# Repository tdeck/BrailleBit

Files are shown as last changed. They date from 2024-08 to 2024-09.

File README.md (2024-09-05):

# BrailleBit - An Arduino braille display

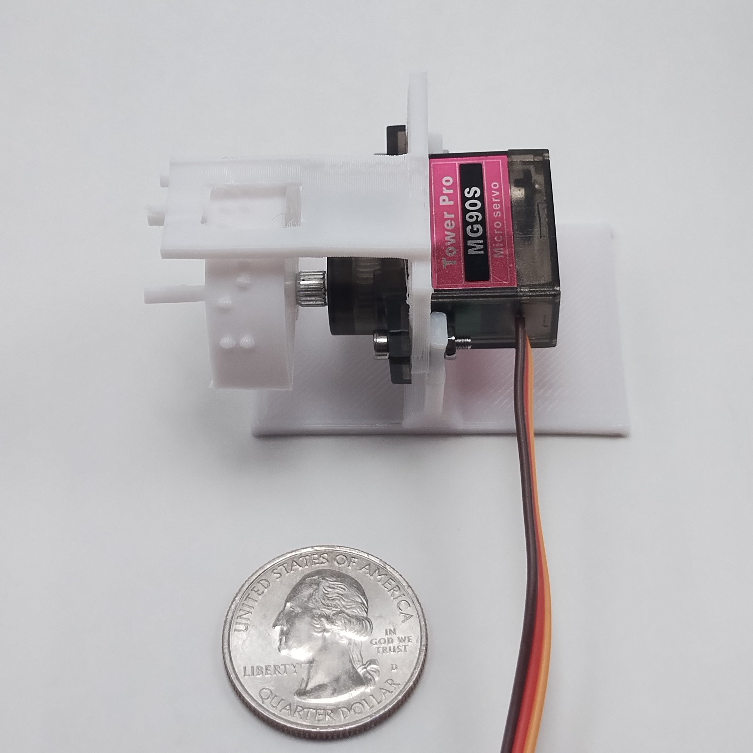
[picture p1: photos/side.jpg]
BrailleBit photo; side

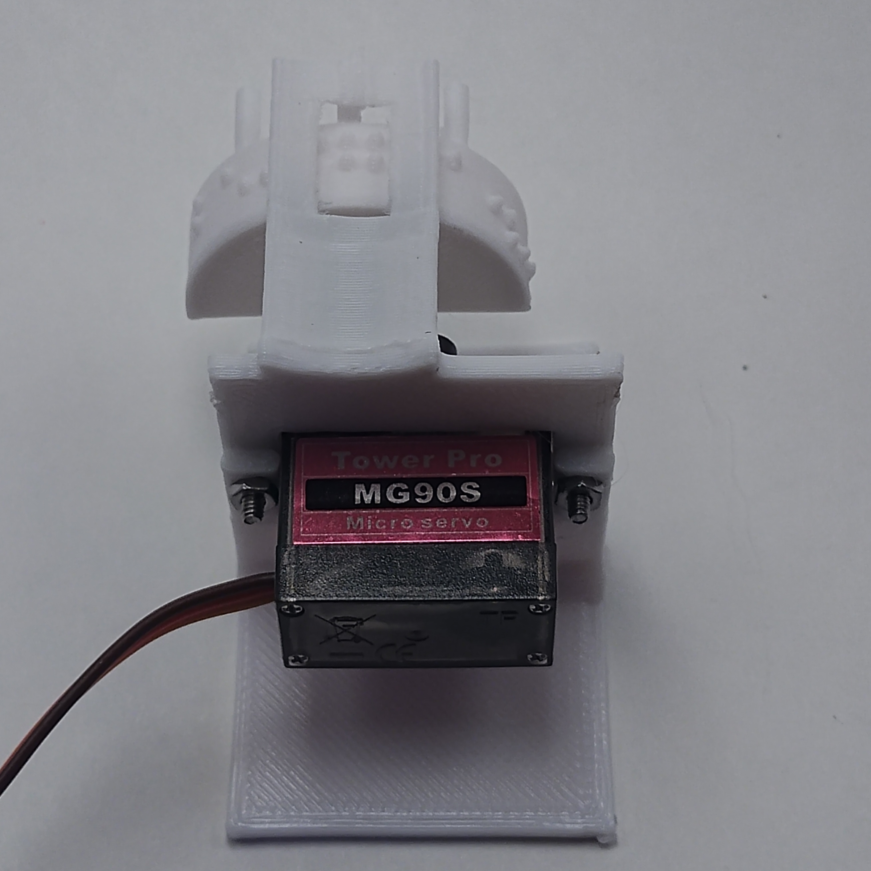
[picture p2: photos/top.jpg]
BrailleBit photo; top


The BrailleBit is an easy way to add a single cell of braille output to your Arduino project. It's cheap and cheerful - using only a hobby servo and 2 or 3 small 3D-printed parts. It costs less than $5, displays standard-sized braille, works with almost any microcontroller, and can be assembled and calibrated by touch. The main drawback is that it's too large to fit multiple cells side-by-side, and has a limited character set. Think of this as an alternative to a 7-segment module, not a replacement for a 2 line LCD.

The hardware is controlled with a simple Arduino library. For example, here's a sketch that repeatedly counts from 0 to 9 with a BrailleBit attached on pin 1:

```cpp
const int SERVO_PIN = ...;

// These come from servo calibration
const uint16_t US_PER_4DEG = ...;
const uint16_t US_CENTER = ...;

const uint16_t US_PER_4COL = US_PER_4DEG * NumericRotor::DEGREES_PER_DOT;
BrailleBit brailleBit(NumericRotor::CHARS);

void setup() {
    brailleBit.attach(SERVO_PIN, US_CENTER, US_PER_4COL);
}

void loop() {
    char* sequence = " 0123456789";

    for (char* ptr = message; ptr != 0; ++ptr) {
        cell.setChar(*p);
        delay(2000);
    } 
}
```

## Physical description

The BrailleBit has a small window through which you can feel two columns of braille dots. Behind this window is the rotor, which is a semicircular plastic piece that has columns of 3 dots in different combinations along its outside wall. A small servo motor allows the BrailleBit to precisely rotate the rotor to expose two adjacent columns of dots at a time. By cleverly arranging the combinations of dots on the rotor's outer wall, we make it possible to display different Braille symbols. The basic BrailleBit is designed for numeric output; it supports letters A-J (for digits 0-9 in braille), the period, minus sign, space, and colon. The result is a device that is about 3.5 cm wide, 6 cm long, and stands 4 cm high on a desk.

The minimalist design of the BrailleBit is a starting point for your own projects and designs. At its simplest, you need the 3D printed rotor and the 3D printed "cover bracket", which provides the fixed window and attaches to a common hobby servo. The base support bracket allows you to place the BrailleBit flat on a desk, with the reading window parallel to the desktop. You can also omit the base bracket and mount the BrailleBit in other ways. For example, you could cut a hole larger than the BrailleBit window in a box, then glue the cover bracket against that hole from the inside.

The provided BrailleBit rotor supports numeric output only. Larger rotors could accommodate more letters, although the process of creating new rotors is not documented yet. A full 26 letter rotor has problems with the mechanical backlash within the servo which I am still working to overcome.

## Parts needed

Here's everything you'll need:

- 3D-printed rotor (prints/rotor.stl)
- 3D-printed cover bracket corresponding to rotor (prints/cover_bracket.stl)
- 3D-printed support bracket (prints/support_bracket.stl) (this is optional, you could mount the BrailleBit another way)
- 2x M2 screws, suggested length 10mm
- 2x m2 nut
- MG90S (or clone) micro servo
- M2.5 5mm screw for servo shaft (this should come with your servo)
- Arduino or compatible microcontroller board

Hardware stores typically don't carry very small screws like this. If you're in the US, I've found [Trimcraft Aviation](http://trimcraftaviation.com/) is a great place to buy small metric fasteners for very little money. M2 screws and nuts are extremely small so it's a good idea to have extras in case you drop one and can't find it again.

The MG90S servo was originally designed by Tower Pro; although there are now many clones available for less than $1 per piece on sites like eBay, Aliexpress, and Banggood. Usually it's more economical to buy a multi-pack. Note that you may end up with a bad batch that drifts or has other problems so consider the cost an your risk tolerance.

### If you don't have a 3D printer

3D printers are common these days at many institutions, including schools and public libraries. There may be one you can use or a service where they'll print things for you for free at these institutions. These parts can be printed on a basic filament 3D printer.

If you are Blind or an educator for Blind people, you may be able to ask the good folks at [See3D](https://see3d.org/) to print these parts for you. Be sure to send them a link to these instructions so they can read the printing notes below.

### Printing notes

Print all parts in their provided orientations.

When slicing the rotor, be sure that the Braille dots are being printed as ripples in the print's outer wall, rather than extra segments attached to the outside. I found that in Cura it was helpful to set the wall thickness to .8mm. I also found printing with thinner layers (.1mm) beneficial for the rotor. Print the rotor without supports.

For the cover bracket, you can print with relatively coarse layers. I recommend enabling supports to fill the window rather than relying on bridging, since the extra material is minimal.

For the support bracket, you don't need any support and can print fast.

## Assembly guide

1. Thread one of the M2 screws through one of the servo's mounting holes so the shaft of the screw points toward the wire end of the servo and away from the rotor.

2. Align the cover bracket with the servo. The servo's shaft is not symmetrical - it is closer to one side of the servo than the other. This is also true of the cover bracket. Slide the cover bracket around the servo and over the protruding screw so that the window in the cover is horizontally aligned with the shaft of the servo. The screw you inserted in step 1 should now pass through the servo mount and then the cover bracket. 

3. If using the base support bracket, slip it onto the screw behind the cover bracket.

4. Attach a nut to the screw and tighten, pushing the bracket(s) so they're flush with the body of the servo.

5. Add the second M2 screw and M2 nut to the other mounting hole and bracket(s) and tighten.

6. With the rotor flat on the table and the semicircular wall pointing upward, insert the servo rotor screw downward into the hole in the rotor. Lift the rotor so the screw pokes through.

7. Screw the protruding rotor screw into the servo shaft and tighten lightly. You make a final adjustment to this screw during the calibration process.

## Attaching the servo to your Arduino (or other microcontroller)

The MG90s servo requires no support circuitry to work with an Arduino. Specifically, you can connect the servo's PWM output directly to a pin on your Arduino that supports PWN, whether 3.3v or 5v. [This page](https://support.arduino.cc/hc/en-us/articles/9350537961500-Use-PWM-output-with-Arduino) lists PWM pins for official Arduino boards; for RP2040 boards like the Pi Pico all pins support PWM.

The servo needs an independent power source. I've had success powering it from the 5 volt USB supply on development boards, but to do this you'll need to account for the large spikes in current draw the servo takes when it moves. A 470 microfarad electrolytic capacitor across the power pins for the servo did the job for me, but if you're having trouble I suggest using a bench power supply at 5 or 6 volts.

### Identifying servo pins

The MG90S has a 3-pin female connector. Near the end of the connector there are 3 small notches on one side, while the other side is flat. With the notched side facing you and the connector pointing down, the pins from left to right are:

- Left (brown): Ground
- Middle (red): Power
- Right (orange): PWM input

Note if you get this backwards, the servo will not work but it also won't be damaged.

## Calibration guide

Calibrating your BrailleBit is necessary before you first use it and after you unscrew or swap the rotor. It's a quick procedure but does require a phillips head screwdriver, a connected Arduino, and 3 pushbuttons wired to I/O pins on the Arduino. Calibration will provide you with two constants `US_CENTER` and `US_PER_4DEG` that are required to control the BrailleBit.

Begin by loading the calibration sketch in the Arduino IDE (firmware/calibration/calibration.ino). You will need to update all pin assignment the constants at the top of the file (SERVO_PIN, LEFT_BUTTON_PIN, CONTINUE_BUTTON_PIN, and RIGHT_BUTTON_PIN).

Wire 3 pushbuttons between V+ and 3 different I/O pins, so that they pull the pins up when pressed. If you're using an RP2040 based board like the Pi Pico you may need external pulldown resistors since the internal ones don't seem to work. As you attach the buttons, update the Arduino sketch to note what pins they're attached to. Wire the servo PWM pin to a free PWM pin (see above) and update that constant as well. Be sure to keep track of which button is "left", "right", and "continue".
 
Upload the sketch to the board and open the serial monitor on your computer. The servo should move, and you'll get a message on the serial monitor telling you to set the center position. The calibration sketch lets you know what mode it's in on the serial console.

The rotor has three little poles sticking up from it, and there's a small tab or spike in the middle of the cover bracket above the window. The goal of the calibration procedure is to teach the Arduino how to line up these tabs.

First, mechanically center the rotor. While the sketch is holding the servo in its default position, partly unscrew the rotor. Hold the *center* tab of the rotor and turn it so it's against the tab on the cover window. Holding these together, tighten the rotor screw firmly. Do not unscrew the rotor again for the rest of the process. Do not skip the mechanical alignment step - the servo cannot rotate a full 360 degrees so we must align the rotor to its range of motion.

It's likely the alignment won't be perfect at this point, so use the left and right buttons to electronically move the rotor until the tabs are aligned as well as you can make them (the smaller window tab should be roughly centered on the rotor tab). At this point you're in coarse alignment mode and the motor will take larger steps. Pressing continue places you in the fine alignment mode where you can fine tune the alignment with smaller steps.

When you have pressed "continue" in the center coarse and fine alignment modes, the servo will swing to where it guesses the left alignment tab will be. Use the left and right buttons to align it to the left tab as well as you can in coarse mode, then press continue to enter fine mode and fine tune it.

When you press "continue" again the servo will swing into position for the final 2 alignment steps - the right coarse and fine alignment.

After you're satisfied with the alignment of the right calibration tab, press the continue button one last time. At this point the calibration sketch will start repeatedly printing values of US_CENTER and US_PER_4DEG to the serial console. Copy these values and save them - they are the goal of the calibration. If you have a problem, you can always power-cycle the Arduino and redo the calibration.

Just as a recap, here are the stages you'll go through in calibration.

1. Center coarse alignment
2. Center fine alignment
3. Left coarse alignment
4. Left fine alignment
5. Right coarse alignment
6. Right fine alignment
7. Output

### Alternatives to the serial console

If your device has no working serial console, there are 2 other ways to get the calibration constants. These can be selected by uncommenting the USE_READOUT_xxx constants in calibration.ino. If your device has EEPROM, you can uncomment USE_READOUT_EEPROM and set a value for EEPROM_WRITE_ADDRESS. The calibration routine will write in two bytes US_CENTER at that address, and US_PER_4DEG two bytes later. You can then use the [EEPROM library](https://docs.arduino.cc/learn/built-in-libraries/eeprom/) to read these values out on the same Arduino board.

Another rather inconvenient option is Morse code. Uncommenting the USE_READOUT_MORSE will cause the servo to dart left to right, sending Morse code. A short dart to the left is a dit (a Morse dot), and a longer dart to the right is a dah (Morse dash). In Morse mode the completed calibration sketch will loop endlessly, sending the morse letter C, then the digits for US_CENTER, then a D, then US_PER_4DEG. Learning morse is beyond the scope of this short tutorial.

## Controlling the BrailleBit

The BrailleBit comes with a simple control library. For now it's not in the Arduino library manager, so start your sketch by copying the code in the firmware/control folder of this repository. That code shows you how to import the BrailleBit and use it in your own projects.

The BrailleBit objects have two control commands: `displayChar()` and `setChar()`. The `setChar()` method simply moves the rotor to the specified character, and if the character hasn't changed it won't move. The `displayChar()` is a bit smarter - if the character is the same as the last one, it will jiggle the servo slightly. This provides important feedback so you can distinguished repeated characters (e.g. "1001" should look different from "101").

You can display more than one character in a couple of ways. The simples is to put a delay between each character output, which is what the example sketch does. A nicer option is to wire up a button that lets you move on to the next character, so that you can suit different users' reading speeds.

## Get in touch!
If you create something cool with the BrailleBit, or have any questions or comments, email me at troy@blindmakers.net. You can also open issues on this GitHub repository. I'd love to share and link to any other creations.

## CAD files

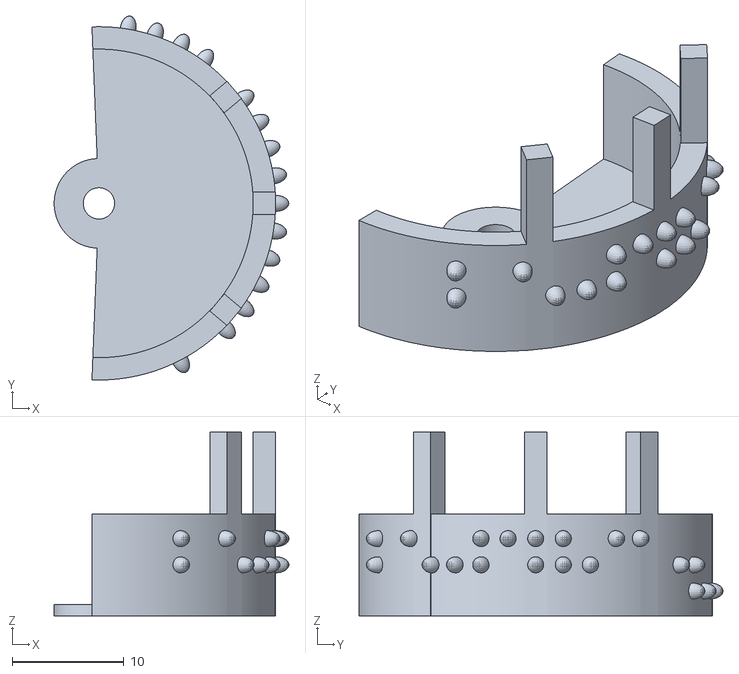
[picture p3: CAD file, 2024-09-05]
prints/rotor.stl
21.0 x 32.5 x 16.4

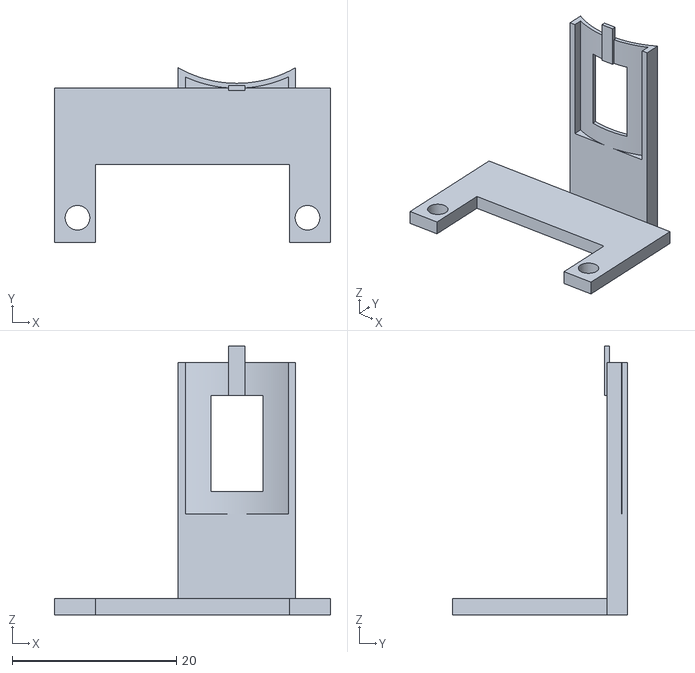
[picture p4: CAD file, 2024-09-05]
prints/cover_bracket.stl
33.6 x 21.3 x 32.7

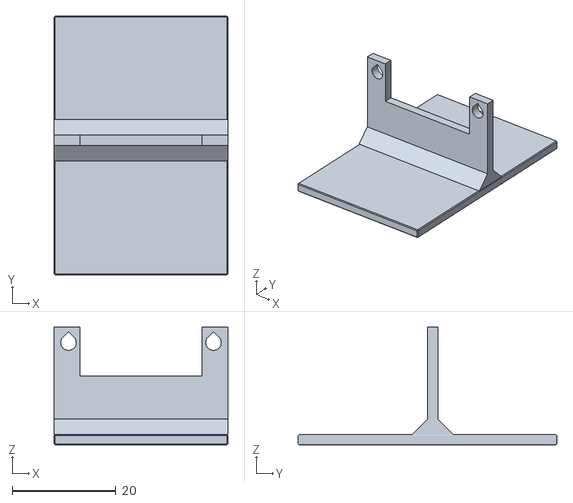
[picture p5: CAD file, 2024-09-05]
prints/support_bracket.stl
33.6 x 50.0 x 22.8

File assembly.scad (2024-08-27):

include <common.scad>

// These movements and rotations just line the assemblies up so their relationship shows up in the preview
forward(radius_of_whole_circle + COVER_ROTOR_GAP)
    right(SERVO_ROTOR_OFF_CENTER)
    up(SERVO_ROTOR_TOP_TO_SCREW_PLATE_BOTTOM)
    down(USE_SERVO_SPLINE ? SERVO_SPLINE_ATTACHMENT_HEIGHT :  0)
    zrot(90)
        braille_rotor();
cover_bracket();

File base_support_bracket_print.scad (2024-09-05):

include <common.scad>

xrot(-90)
base_support_bracket();

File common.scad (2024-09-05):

include <BOSL/constants.scad>
use <BOSL/transforms.scad>
use <BOSL/shapes.scad>

// The next long line was generated from a Python script and represents the arrangement of 3-dot columns on the rotor wall
// All possible cells
//DOT_COLUMNS = [[0,0,0],[1,0,0],[0,1,1],[0,0,1],[0,0,0],[1,1,1],[0,0,1],[1,0,1],[0,1,1],[1,1,1],[1,0,1],[1,0,0],[1,1,0],[1,1,1],[1,1,0],[0,0,0],[0,0,1],[1,1,0],[1,0,1],[1,0,1],[0,0,0],[0,1,1],[1,0,1],[1,1,0],[0,1,0],[0,1,0],[1,0,0],[1,0,1],[0,0,1],[1,1,1],[1,0,0],[0,0,0],[1,1,0],[1,1,0],[0,0,1],[1,0,0],[0,1,0],[1,0,1],[0,1,0],[0,0,1],[0,0,1],[0,1,1],[0,1,1],[1,0,0],[0,0,1],[0,1,0],[1,1,0],[0,1,1],[1,1,0],[1,0,0],[1,0,0],[1,1,1],[1,1,1],[0,1,1],[0,1,0],[0,1,1],[0,0,0],[0,0,0],[1,0,1],[1,1,1],[0,0,0],[0,1,0],[1,1,1],[0,1,0],[0,0,0]];
// Alpha + basic punctuation
//DOT_COLUMNS = [[0,0,0],[0,0,1],[1,1,1],[0,0,0],[0,0,0],[0,1,1],[0,0,1],[0,0,1],[1,1,1],[0,1,0],[0,1,1],[1,1,0],[0,0,0],[0,1,0],[0,0,0],[1,0,1],[0,1,0],[1,1,0],[1,0,0],[0,1,0],[1,0,0],[1,0,0],[1,1,0],[1,1,0],[0,1,0],[1,1,1],[1,0,0],[0,0,0],[1,0,1],[1,0,1],[1,1,1],[1,1,0],[1,0,1],[1,1,0],[1,0,1],[1,0,0],[1,0,1],[0,1,1],[1,0,0],[1,1,1],[0,0,1],[1,0,1],[0,0,0],[1,0,1],[0,0,1]];

// Numeric
//DOT_COLUMNS = [[0,0,0],[0,0,0],[1,1,0],[0,1,0],[1,0,0],[1,0,0],[0,1,0],[0,1,1],[1,0,0],[1,1,0],[1,1,0],[0,0,0],[0,1,0],[1,1,0],[1,0,0],[0,0,0],[0,0,1],[0,0,1]];

// Numeric with colon
DOT_COLUMNS = [[0,0,0],[0,0,0],[1,1,0],[0,0,0],[1,0,0],[0,1,0],[0,1,0],[1,1,0],[1,0,0],[1,1,0],[1,1,0],[0,1,0],[1,0,0],[1,0,0],[0,0,0],[0,1,0],[0,1,1],[0,0,1],[0,0,1]];

// All dots filled, variable size for debugging
//DOT_COLUMNS =  [for(i=[1:5])([1,1,1])];

// Braille dimensions
DOT_HEIGHT = 1.2;  // Official is .48 but that's hard to feel, so I used the max height from California sign standards
DOT_DIAM = 1.44;
DOT_SPACING = 2.34; // Center to center

// DEGREES_TO_POPULATE specifies how much of the circle's arc can be "addressed" by the servo.
// I recommend adding a buffer zone so that the disc doesn't have to be perfectly aligned to the servo's movement
// region (e.g. for a 180 degree servo a 170 degree DEGREES_TO_POPULATE lets yo fix a 10 degree difference in
// software calibration rather than in hardware.
DEGREES_TO_POPULATE = 170;

// Rotor stuff
BLANK_SPACE_AT_END = 2; // Blank space to leave before first col and after last col on wheel (set to 0 for 360 deg)
V_PADDING = 1.5;
ROTOR_WALL_THICKNESS = 2;

// Backlash spring stuff
USE_BACKLASH_SPRING = false; // True is recommended unless your servo has very little play or your rotor radius is small
BACKLASH_SPRING_HORN_LENGTH = 15;
BACKLASH_SPRING_HORN_WIDTH = 6;

// Servo stuff
SERVO_RECT_HOLE_WIDTH = 23.6;
SERVO_RECT_HOLE_DEPTH = 13.0;
SERVO_HOLE_TO_SCREW_HOLE_CENTER = 2.2;
SERVO_MOUNTING_SCREW_HOLE_DIAM = 3.0;
SERVO_ROTOR_OFF_CENTER = 5.4;
SERVO_ROTOR_TOP_TO_SCREW_PLATE_BOTTOM = 11.9 + 2.4;
SERVO_HUB_SCREW_HOLE_DIAM = 2.8; // Should be a little on the small side so screw holds the rotor snugly
SERVO_SPLINE_TEETH = 20;
SERVO_SPLINE_TOOTH_DEPTH = .3;
SERVO_SPLINE_OUTER_DIAMETER = 4.9;
SERVO_SPLINE_CLEARANCE = .16; // Adjust this if your print doesn't fit
SERVO_SPLINE_ATTACHMENT_HEIGHT = 4;
SERVO_SPLINE_ATTACHMENT_WALL = 3; // Not exact, make a bit larger than it needs

// TODO the spline doesn't fit reliably when printed; explore attaching to servo horns
USE_SERVO_SPLINE = USE_BACKLASH_SPRING; // Recommended if you use the backlash spring; makes centering a little more difficult

// Window/cover stuff
COVER_RADIUS = 15;
COVER_WALL_THICKNESS = .6;
COVER_WINDOW_WIDTH = DOT_SPACING * 2.7;
COVER_WINDOW_HEIGHT = DOT_SPACING * 5;
COVER_WALL_ABOVE_WINDOW = 4;
COVER_WALL_BESIDE_WINDOW = 4; // This is not permiter length, it's cartesian
COVER_ROTOR_GAP = 0; // Extra gap between end of dots and start of cover with window in it
COVER_BRACKET_THICKNESS = 2;
COVER_FOOT_DEPTH = 5; // TODO figure out what this really means; it doesn't seem to be using the full 5
COVER_FOOT_HEIGHT = SERVO_ROTOR_TOP_TO_SCREW_PLATE_BOTTOM - 2;
COVER_BRACKET_LEN_PAST_SERVO_CENTER = 3;
COVER_BRACKET_LEN_PAST_SERVO_SIDES = 5;
COVER_BRACKET_WIRE_NOTCH_DEPTH = 2;
COVER_BRACKET_WIRE_NOTCH_WIDTH = 4;
COVER_SIDE_PILLAR_SIZE = 1.8;  // TODO make this not need trial and error

assert(COVER_BRACKET_WIRE_NOTCH_DEPTH < COVER_BRACKET_LEN_PAST_SERVO_SIDES);

// Floor
ROTOR_FLOOR_THICKNESS = 1;
ROTOR_HUB_RADIUS = 4;

// Calbiration tabs
USE_CALIBRATION_TABS = true; // This adds a little bit of plastic but makes aligning and calibrating your servo 10 times easier
CALIBRATION_TAB_ANGLE = 40;
CALIBRATION_TAB_HEIGHT = 2; // This is height above the window; height above the rotor will be greater
CALIBRATION_TAB_WIDTH = 2;
ROTOR_CALIBRATION_TAB_DEPTH = 2;

BOTTOM_CHAMFER_WIDTH = .2; // Used in some places to avoid elephants foot

// Support bracket
SUPPORT_BRACKET_EXTRA_HEIGHT = 2;
SUPPORT_BRACKET_BASE_LENGTH = 50;
SUPPORT_BRACKET_CHAMFER = 3; // Added in addition to the width of the wall

// Utility constants
ARBITRARY = 1000; // Arbitrary size for various hole dimensions
SMALL_DELTA = .01; // Small movement to resolve ambiguity when part edges overlap

 // Set global params for smoother shapes
$fa = 1;
$fs = .2;

// Computed constants
perimeter_needed_for_dots = (len(DOT_COLUMNS) + 1) * DOT_SPACING; // DOT_SPACING is center-to-center
perimeter_of_whole_circle = perimeter_needed_for_dots * 360 / DEGREES_TO_POPULATE;
radius_of_whole_circle = perimeter_of_whole_circle / PI / 2;
cell_height = 2*DOT_SPACING + DOT_DIAM;
rotor_height = cell_height + 2*V_PADDING;
cover_width = COVER_WINDOW_WIDTH + 2 * COVER_WALL_BESIDE_WINDOW;
cover_wall_above_rotor = COVER_WALL_ABOVE_WINDOW - (rotor_height - COVER_WINDOW_HEIGHT) / 2;

echo("len(DOT_COLUMNS)", len(DOT_COLUMNS));

module servo_spline_carveout(clearance=SERVO_SPLINE_CLEARANCE) {
    // This isn't a partuclarly well modeled socket for the servo spline but it manages
    // to work anyway
    spline_circumference = PI * SERVO_SPLINE_OUTER_DIAMETER;
    tooth_pitch_degrees = 360 / SERVO_SPLINE_TEETH; // This is for the tip + root
    orig_tooth_tip_mm = spline_circumference / SERVO_SPLINE_TEETH / 2;
    
    carveout_diameter = SERVO_SPLINE_OUTER_DIAMETER - 2 * SERVO_SPLINE_TOOTH_DEPTH + 2 * clearance;
    // Hole sized to fit around the spline if the teeth were missing (i.e. filed off)
    zcyl(
        d=carveout_diameter,
        h=SERVO_SPLINE_ATTACHMENT_HEIGHT,
        align=V_UP
    );
    
    // Slots to accommodate the teeth
    tooth_radius = SERVO_SPLINE_OUTER_DIAMETER/2 + clearance;
    for (i = [0: SERVO_SPLINE_TEETH - 1]) {
        zrot(i * tooth_pitch_degrees)
        cuboid(
            [
                tooth_radius,
                orig_tooth_tip_mm, //+ 2 * SERVO_SPLINE_CLEARANCE,
                SERVO_SPLINE_ATTACHMENT_HEIGHT
            ],
            align=V_UP + V_RIGHT
        );
    }
    
    // Bottom chamfer to avoid problems with elephants foot
    chamfer_outer_radius = tooth_radius + BOTTOM_CHAMFER_WIDTH;
    zcyl(
        d2=carveout_diameter,
        r1=chamfer_outer_radius,
        h=chamfer_outer_radius - (carveout_diameter / 2),
        align=V_UP
    );
}


module braille_rotor() {
    degrees_per_dot = DEGREES_TO_POPULATE / len(DOT_COLUMNS);
    
    echo("Computed diameter", radius_of_whole_circle * 2, "mm");
    echo("Degrees per dot", degrees_per_dot);
    
    module braille_arc() {
        // This is a shape that can be intersected with the support rotor to make it less than 360 degrees
        blank_space_angle = BLANK_SPACE_AT_END / perimeter_of_whole_circle * 360;
        arc_degrees = DEGREES_TO_POPULATE + 2*blank_space_angle;
        module arc_mask() {
            zrot(-arc_degrees/2) 
                pie_slice(
                    h=100, // Arbitrarily large
                    r=radius_of_whole_circle,
                    ang=arc_degrees
            );
        }
        echo("Arc degrees:", arc_degrees); // TODO debug
        
        // This rotation corrects the angle so it's symmetical about the x axis

        // Create the base shape with the arc supporting the dots
        intersection() {
            union() {
                // Draw a base
                zcyl(r=radius_of_whole_circle, l=ROTOR_FLOOR_THICKNESS, center=false);
                // Draw a side
                tube(h=rotor_height, or=radius_of_whole_circle, wall=ROTOR_WALL_THICKNESS);
            };
            arc_mask();
        }
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

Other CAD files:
cover_bracket_print.scad
rotor_print.scad
spline_clearance_tests.scad

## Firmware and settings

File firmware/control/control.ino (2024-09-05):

#include "BrailleBit.h"

const int SERVO_PIN = 26;

// These come from servo calibration
const uint16_t US_PER_4DEG = 48;
const uint16_t US_CENTER = 1520;

// Derived constants; do not change
// Note: Here this is calculated at compile time.
// If you do this calculation dynamically (rather than in a const), you may end
// up including floating point functions and making your code larger!
const uint16_t US_PER_4COL = US_PER_4DEG * NumericRotor::DEGREES_PER_DOT;

BrailleBit cell(NumericRotor::CHARS);

const int CONTINUE_BUTTON_PIN = 1;

void setup() {
  cell.attach(SERVO_PIN, US_CENTER, US_PER_4COL);

  pinMode(CONTINUE_BUTTON_PIN, INPUT_PULLDOWN);
  Serial.begin(9600);
  delay(2000); // Give the serial device time to get set up
}

void loop() {
  // This code prints a random digit 1-9 to both the BrailleBit and the serial console
  // each time the continue button is pressed.
  static char continue_button_history = 0;
  static bool ready_for_press = 0;

  continue_button_history = (continue_button_history << 1) | digitalRead(CONTINUE_BUTTON_PIN);
  if (continue_button_history == 0) ready_for_press = true;

  if (ready_for_press && continue_button_history == 0xFF) {
    ready_for_press = 0;
    char c = '1' + random(0, 8);
    Serial.println(c);
    cell.displayChar(c);
  }

  delay(10);
}

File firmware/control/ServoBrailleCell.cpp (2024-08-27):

#include "ServoBrailleCell.h"
#include <string.h>

// NOTE: We assume rotorChars is a string constant and not going to go away,
// which is valid most of the time for microcontroller code, so we don't copy it.
ServoBrailleCell::ServoBrailleCell(const char* rotor_chars): rotor_chars_(rotor_chars) {}

void ServoBrailleCell::attach(int pin, uint16_t us_center, uint16_t us_per_4_cols) {

  int rotor_positions = strlen(rotor_chars_);
  int mid_pos = rotor_positions / 2;
  first_col_us_ = 
    us_center + 
    ((mid_pos * us_per_4_cols) >> 2); // >> 2 divides by 4

  // An even number of characters means an odd number of dot columns.
  // For a drum with an odd number of dot columns, the central calibration tab
  // will be directly above a line of dots, so we must rotate 1/2 step to have
  // 2 columns in the window and display the character.
  if (rotor_positions % 2 == 0) {
    first_col_us_ -= us_per_4_cols >> 3; // >> 3 divides by 8
  }

  us_per_4_cols_ = us_per_4_cols;

  servo.attach(pin);
}

void ServoBrailleCell::setChar(char c) {
  if (us_per_4_cols_ == 0) return; // Not initialized yet

  int16_t us_from_start_times_4 = 0;
  for (const char * rcp = rotor_chars_; *rcp != 0; ++ rcp) {
    if (*rcp == c) {
        uint16_t us = first_col_us_ + (us_from_start_times_4 >> 2);
        // TODO some kind of backlash compensation
        servo.writeMicroseconds(us);
    }

    us_from_start_times_4 -= us_per_4_cols_;
  }
}

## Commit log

2024-02-26 First versino of wheel, no hub, dots print poorly
    [horiz_braille_wheel.scad]
2024-02-26 Spherical dots + proper v-padding
    [horiz_braille_wheel.scad]
2024-02-27 Fix big dot height mistake
    [horiz_braille_wheel.scad]
2024-02-27 First decent feeling print!
    [horiz_braille_wheel.scad]
2024-02-27 Naive first window
    Too small to get my finger in and feel the dots. Also the code is a bit
    more spaghetti now but I can clean that up if this concept works out.
    Cover printed quite nicely in vertial pos, no strings or droop!
    [horiz_braille_wheel.scad]
2024-04-16 Reasonably readable version
    G will be in the middle o the wheel per script changes
    Print the cover with supports for best results (window sag can make it
    harder to read)
    [horiz_braille_wheel.scad]
2024-04-18 First WIP control program using angles
    Single degrees per dot doesn't have enough resolution, so that chars
    at the end of the drum (even a small numeric drum) are offset wrong. But
    this somewhat works.
    Going to change to a higher resolution approach.
    [control.ino]
2024-04-19 Updated 6dot_drum script to use Braille ASCII
    This script now outputs constants that should be copyable directly into
    OpenScad and and Arduino sketch, including the CELL_CHARS string that
    provides the ordering of Braille ASCII characters to drum positions.
2024-04-24 Kinda working alphanumeric
    Remaining issues:
    - Ends beyond servo range
    - Alignment needs to be better
    - Backlash not fully solved, have a hack for it
    [horiz_braille_wheel.scad]
2024-08-15 More precision using us x 4; needs cleanup + backlash comp
    [control.ino]
2024-08-15 Tweaks; not sure if tried or printed yet
    [horiz_braille_wheel.scad]
2024-08-15 Add spring horn
    [horiz_braille_wheel.scad]
2024-08-16 Add wire notch in backlash spring mode
    [horiz_braille_wheel.scad]
2024-08-16 ++wire notch; WIP cal tabs; code cleanup
    [horiz_braille_wheel.scad]
2024-08-16 Shifted bracket spring horn; Drum cal tab WIP
    Planning to add a servo horn. Now that I have a backlash spring there's
    force on the drum that causes the hub screw to unscrew.
    [horiz_braille_wheel.scad]
2024-08-19 Checkin to print numeric
    [horiz_braille_wheel.scad]
2024-08-19 Cover calibration tab; rm COVER_SIDE_PILLAR_BACK
    [horiz_braille_wheel.scad]
2024-08-21 Calibration working + tested
    Tested everything but EEPROM, which the RP2040 doesn't have.
    [calibration.ino]
2024-08-21 Cleaned up calibration code; should be done
2024-08-22 Definite WIP on angular alignment
    [horiz_braille_wheel.scad]
2024-08-22 Now cal tabs are in a consistent place wrt dots
    For rotors with an even number of columns, they are between 2 coloms. For
    rotors with an odd number of columns, they are centered on a column.
    [horiz_braille_wheel.scad]
2024-08-22 Small cleanups
    [horiz_braille_wheel.scad]
2024-08-22 Fixed numeric drum including A
    [horiz_braille_wheel.scad]
2024-08-22 Rename drum/rotor in SCAD; taller dot test
    [horiz_braille_wheel.scad]
2024-08-22 Fixes + even taller dots
    [horiz_braille_wheel.scad]
2024-08-23 Numeric works well!
    Added serial test that prints to both braille display & serial; felt it
    and tested it.
2024-08-26 WIP spline using rectangular gear slots
    [horiz_braille_wheel.scad]
2024-08-27 Still trying to get spline to fit
    [horiz_braille_wheel.scad]
2024-08-27 Split files; fix issue with backalsh bracket length
    The bracket length around the far side of the servo in backlash spring
    configuration was wrong bc it was based on the hub radius.
    [assembly.scad, common.scad, cover_bracket_print.scad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]
2024-08-27 Spline clearance tests
    [common.scad, horiz_braille_wheel.scad, spline_clearance_tests.scad]
2024-08-27 Fix clearance test
    [common.scad, spline_clearance_tests.scad]
2024-08-27 Adjust window height when using spline
    [assembly.scad, common.scad]
2024-08-27 About to try new spline rotor
    [common.scad]
2024-08-28 WIP can't figure out spline fit
    I am really struggling to figure out why the spline fit test result
    doesn't translate to the rotor print.
    [common.scad]
2024-08-28 Revert debugs + fix cal tab
    [common.scad]
2024-09-04 Rename lib to BrailleBit; add numeric rotor consts
2024-09-05 Lots of improvements
    - Bottom support bracket
    - New numeric drum with colon
    - Various cleanups
    [common.scad]
2024-09-05 Add base support print
    [base_support_bracket_print.scad]
2024-09-05 Add readme and numeric STLs
    [cover_bracket.stl, rotor.stl, support_bracket.stl]
